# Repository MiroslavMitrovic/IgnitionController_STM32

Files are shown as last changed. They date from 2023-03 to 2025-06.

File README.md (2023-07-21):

# IgnitionController_STM32

## Ignition controller implementation for  4T Single Cylinder/V-Twin motorcycle. 

- Generated documentation is available in .\IgnitionController_STM32\Documentation\Ignition_Controller.chm
- Requirements are available in .\IgnitionController_STM32\Design\Requirements\IgnitionControllerRequriements.txt
- Architecture is done with Rational Software architect, and project is available at .\IgnitionController_STM32\Design\

## Addition of CMake build toolchain 
- Command for build configuration generation is : 
cmake -G "Unix Makefiles" -S . -B build -DCMAKE_BUILD_TYPE="Debug" -DCMAKE_TOOLCHAIN_FILE="arm-none-eabi-gcc.cmake" -DCMAKE_EXPORT_COMPILE_COMMANDS=1 
- Command for build is : 
cmake --build build
## Addition of Static and Dynamic Test Frameworks 
- For Static Code Analysis Mathworks Polyspace Code Prover and Bug finder tools are used 
- For Dynamic(Unit) Testing Google Test Framework is used 
- Setup is available in Testing Folder.

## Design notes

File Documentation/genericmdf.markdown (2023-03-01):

Design Document
===============
Project:Ignition Controller \n
Version: v1.00.00 \n

Table of Contents
-----------------

@subpage Description

@subpage TermsAndAbbreviations 

@subpage Resources 

@subpage Exceptions 

@subpage Tests 

@subpage Links 

@page Description
Description 
==============================

# Ignition Controller for 2 Cylinder Bike
Ignition controller powered by STM32F407VGT6 MCU. 
## Implementation 
-	RPM is calculated out of Sensor input from Crank or Cam shaft
-	Firing of cylinders is performed in scheduled manner via FSM handling.
## Architecture Display 
### File Structure
@image html IgnitionController_IgnitionControlerFileStructure.png
### Dependencies
@image html IgnitionController_IgnitionControlerStructure.png
### Activity Diagram 
@image html IgnitionController_IgnitionControllerActivityDiagram.png
### FSM Diagrams 
@image html IgnitionController_StatemachineDiagram1.png
@image html IgnitionController_StatemachineDiagram1_1.png
### Class Diagram
@image html IgnitionController_IgnitonControllerClasses.png
### Use Case Diagram 
@image html IgnitionController_UsecaseDiagram_IgnitionControl.png

@page TermsAndAbbreviations
Terms And Abbreviations 
=============================
**Ignition Controller is licensed under the GNU General Public License v3.0**
Permissions of this strong copyleft license are conditioned on making available complete source code of licensed works and modifications, which include larger works using a licensed work, under the same license. Copyright and license notices must be preserved. Contributors provide an express grant of patent rights.

####Permissions
-	Commercial use
-	 Modification
-	 Distribution
-	Patent use
-	 Private use
####Limitations
-	 x Liability
-	 x Warranty

@page Resources
Resources
============================
**RAM Consumption**
- 1.79kB used out of 128kB

**ROM Consumption**

- 17.51kB used out of 1024kB 

@page Exceptions
Exception and Error Handling
============================
If error occurs error handler will put MCU in infinite loop and application will not function.

@page Tests
# Dynamic Tests
- Dynamic Tests are available in folder Testing/Dynamic Testing. GTEST framework is used for unit testing. 
============================

@page Links 
**Links**
-  Link to the repo is [Ignition Controller](https://github.com/MiroslavMitrovic/IgnitionController_STM32.git).

============================

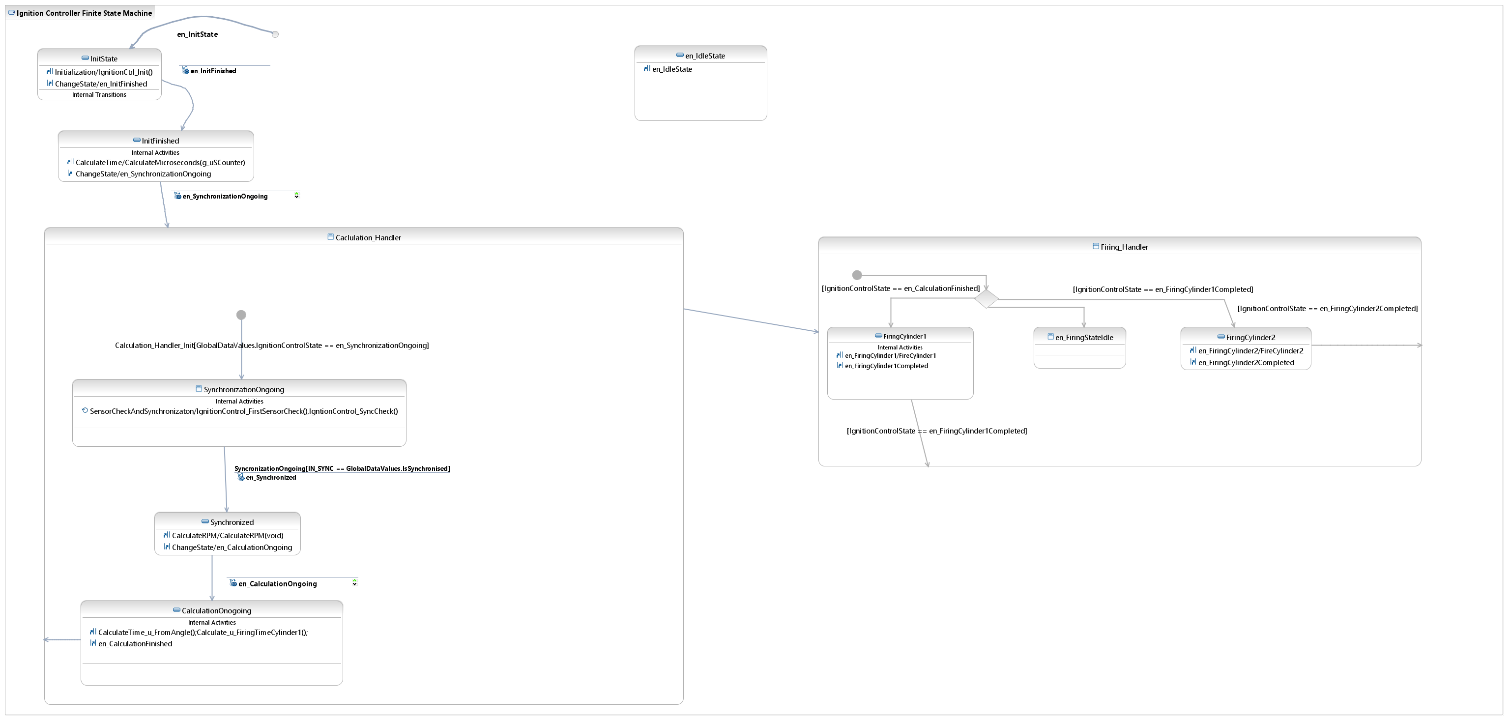
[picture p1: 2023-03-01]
Design/IgnitionController_IgnitionControllerFiniteStateMachineDiagram.png

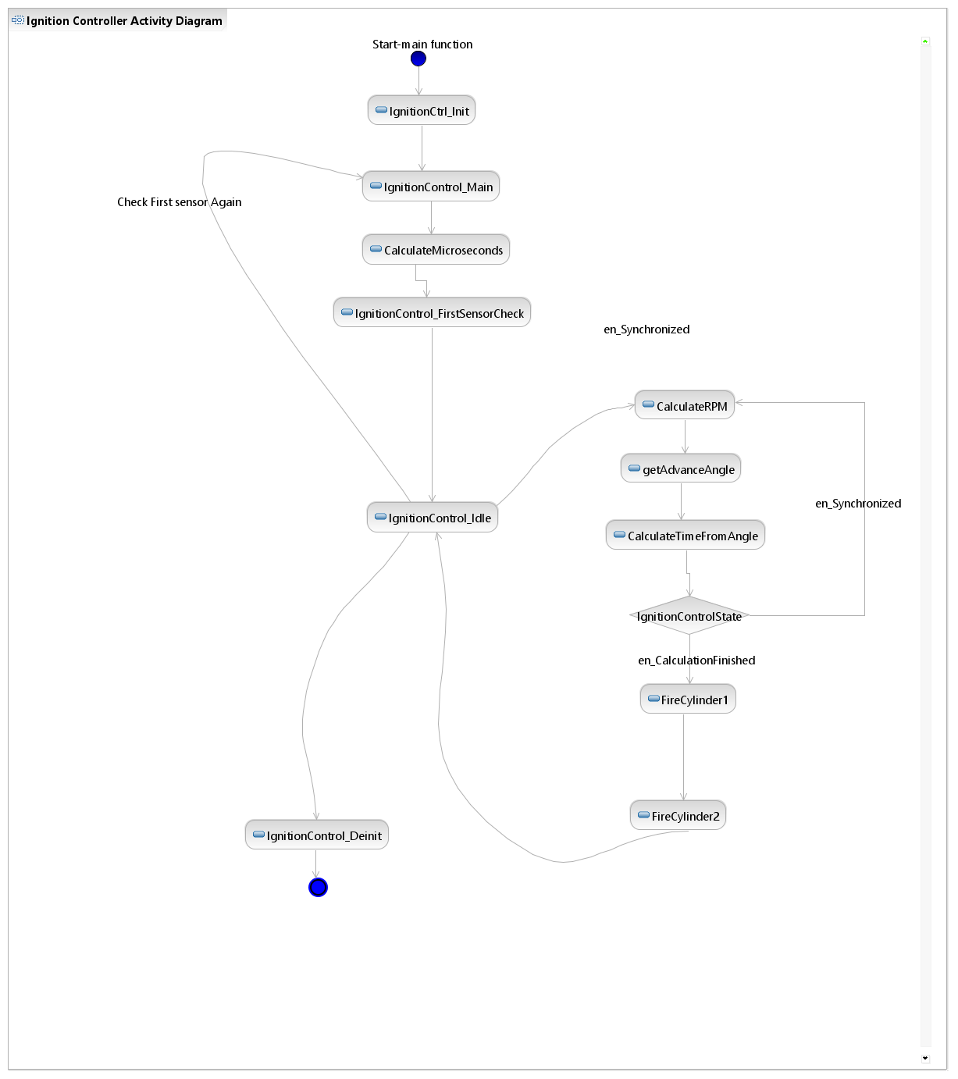
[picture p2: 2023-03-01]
Design/IgnitionController_IgnitionControllerActivityDiagram.png

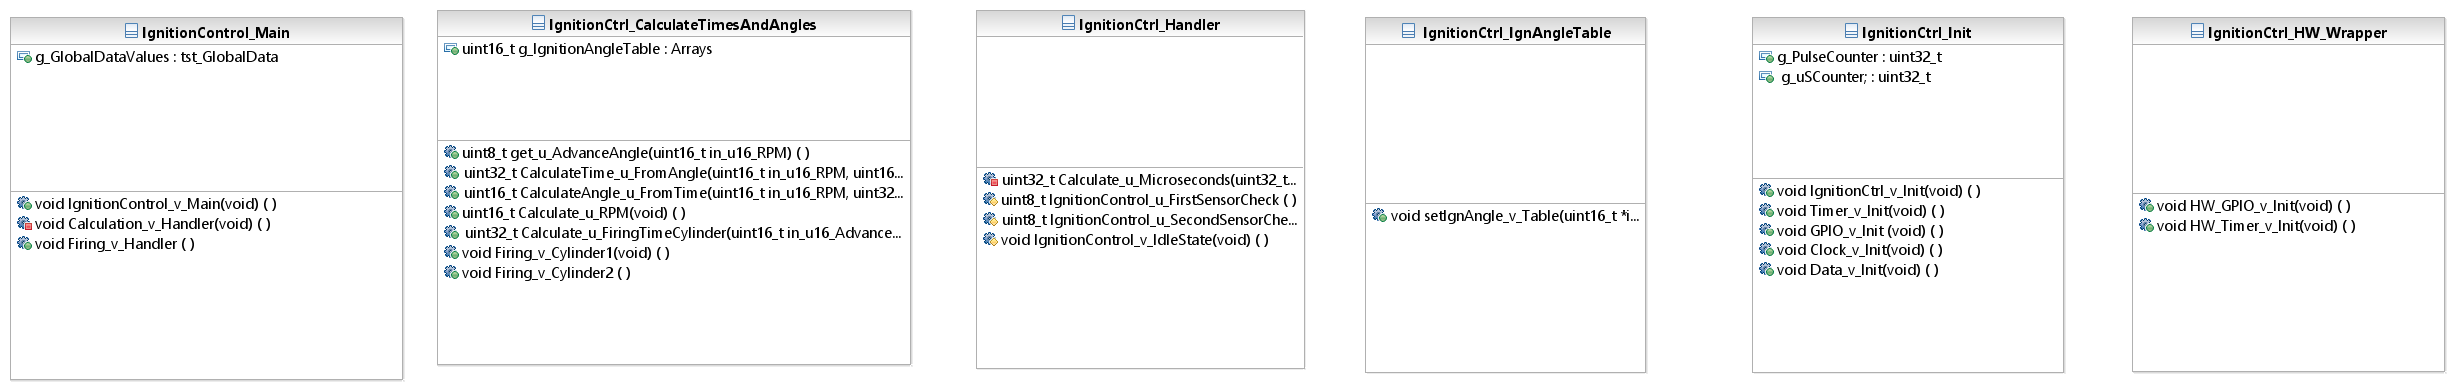
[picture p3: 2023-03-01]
Design/IgnitionController_IgnitonControllerClasses.png

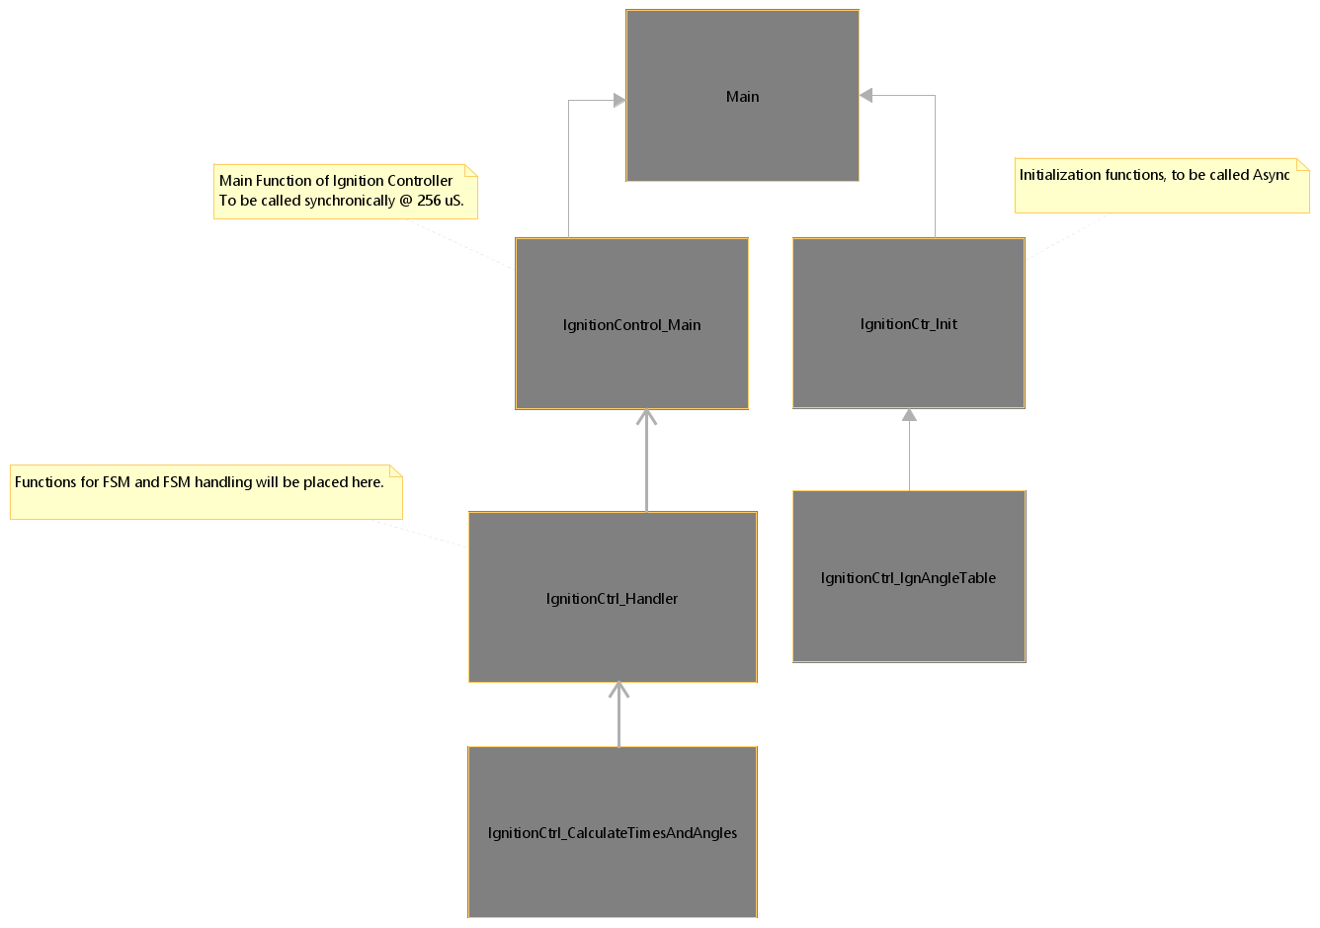
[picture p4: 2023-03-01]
Design/IgnitionController_IgnitionControlerStructure.png

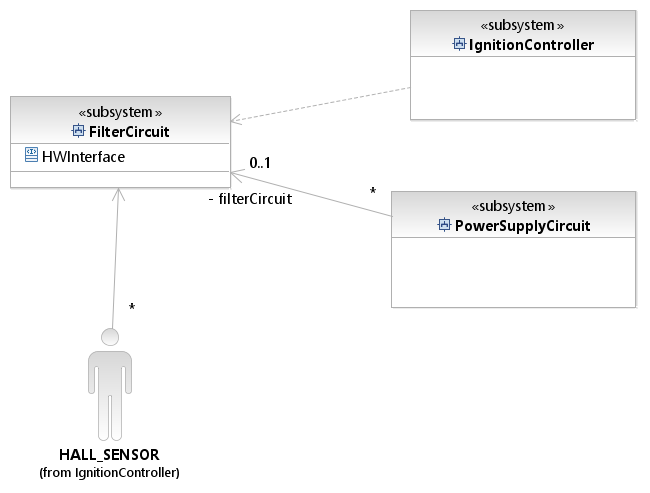
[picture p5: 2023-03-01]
Design/IgnitionController_UsecaseDiagram_IgnitionControl.png

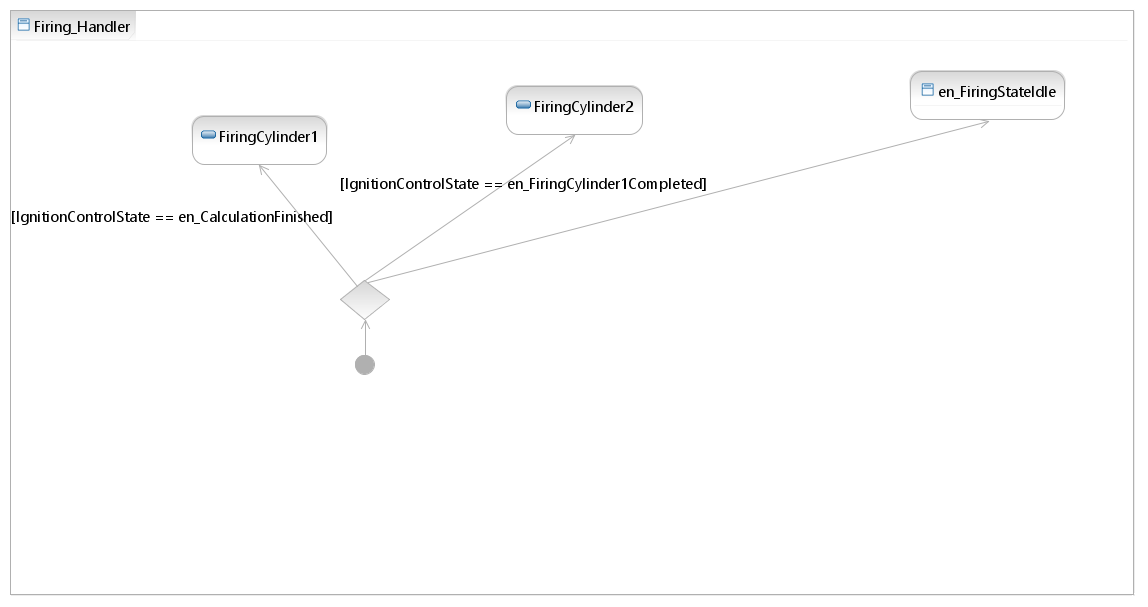
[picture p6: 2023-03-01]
Design/IgnitionController_StatemachineDiagram1_1.png

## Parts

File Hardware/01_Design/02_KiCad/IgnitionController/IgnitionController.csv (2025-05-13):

Reference | Qty | Value | DNP | Exclude from BOM | Exclude from Board | Footprint | Datasheet
C1,C2,C3,C4,C5,C13 | 6 | 100n |  |  |  | Capacitor_SMD:C_0805_2012Metric_Pad1.18x1.45mm_HandSolder | ~
C6,C9,C11 | 3 | UCL1V101MNL1GS |  |  |  | Capacitor_SMD:CP_Elec_8x11.9 | ~
C7 | 1 | 100u |  |  |  | Capacitor_SMD:C_0805_2012Metric_Pad1.18x1.45mm_HandSolder | ~
C8,C10,C12 | 3 | UCL1V331MNL1GS |  |  |  | Capacitor_SMD:CP_Elec_10x12.5 | ~
C14,C15 | 2 | 22p |  |  |  | Capacitor_SMD:C_0805_2012Metric_Pad1.18x1.45mm_HandSolder | ~
C16,C17,C18,C19 | 4 | 12p |  |  |  | Capacitor_SMD:C_0805_2012Metric_Pad1.18x1.45mm_HandSolder | ~
C20,C22,C24,C26,C28,C30,C32,C34,C36,C40,C42 | 11 | 0.1u |  |  |  | Capacitor_SMD:C_0805_2012Metric_Pad1.18x1.45mm_HandSolder | ~
C21,C23,C25,C27,C29,C31,C33,C35,C39,C41 | 10 | 1u |  |  |  | Capacitor_SMD:C_0805_2012Metric_Pad1.18x1.45mm_HandSolder | ~
C37,C38 | 2 | 2.2uF |  |  |  | Capacitor_SMD:C_0805_2012Metric_Pad1.18x1.45mm_HandSolder | ~
D3,D4,D5,D19,D20,D21,D22 | 7 | RED |  |  |  | LED_SMD:LED_1206_3216Metric_Pad1.42x1.75mm_HandSolder | ~
D6,D7,D17,D18 | 4 | SM6T100A |  |  |  | Diode_SMD:D_SMB | https://www.st.com/resource/en/datasheet/sm6t.pdf
D8 | 1 | BZX84B16VLY |  |  |  | Package_TO_SOT_SMD:SOT-23 | https://diotec.com/tl_files/diotec/files/pdf/datasheets/bzx84c2v4.pdf
D9,D13,D15 | 3 | SS14 |  |  |  | Diode_SMD:D_SMA | https://www.vishay.com/docs/88746/ss12.pdf
D10 | 1 | KDZV18B |  |  |  | Diode_SMD:D_SOD-123 | ~
D11,D14,D16 | 3 | RED |  |  |  | LED_SMD:LED_0805_2012Metric_Pad1.15x1.40mm_HandSolder | ~
D12 | 1 | BZX84C18VLY |  |  |  | Package_TO_SOT_SMD:SOT-23 | https://diotec.com/tl_files/diotec/files/pdf/datasheets/bzx84c2v4.pdf
F1 | 1 | 2A Fuse |  |  |  | Fuse:Fuse_0805_2012Metric_Pad1.15x1.40mm_HandSolder | ~
L3,L4,L5 | 3 | L_Iron |  |  |  | Inductor_SMD:L_7.3x7.3_H3.5 | ~
Q1,Q7 | 2 | SS8050 |  |  |  | Package_TO_SOT_SMD:TSOT-23_HandSoldering | http://www.secosgmbh.com/datasheet/products/SSMPTransistor/SOT-23/SS8050.pdf
Q2,Q3 | 2 | DMP6050SSD |  |  |  | Package_SO:SOIC-8_3.9x4.9mm_P1.27mm | https://www.diodes.com/assets/Datasheets/DMP6050SSD.pdf
Q4 | 1 | RSJ250P10 |  |  |  | Package_TO_SOT_SMD:TO-263-2 | https://ngspice.sourceforge.io/docs/ngspice-html-manual/manual.xhtml#cha_MOSFETs
Q5 | 1 | BC856 |  |  |  | Package_TO_SOT_SMD:SOT-23 | https://www.onsemi.com/pub/Collateral/BC860-D.pdf
Q6 | 1 | IRF9Z34NSPbF |  |  |  | Package_TO_SOT_SMD:TO-263-2 | https://ngspice.sourceforge.io/docs/ngspice-html-manual/manual.xhtml#cha_MOSFETs
Q8,Q9,Q10,Q11 | 4 | IRF540N |  |  |  | Package_TO_SOT_THT:TO-220-3_Vertical | http://www.irf.com/product-info/datasheets/data/irf540n.pdf
R1,R4,R28 | 3 | 10k |  |  |  | Resistor_SMD:R_0805_2012Metric_Pad1.20x1.40mm_HandSolder | ~
R2 | 1 | 510R |  |  |  | Resistor_SMD:R_0805_2012Metric_Pad1.20x1.40mm_HandSolder | ~
R3,R16,R17,R18,R19 | 5 | 0R |  |  |  | Resistor_SMD:R_0805_2012Metric_Pad1.20x1.40mm_HandSolder | ~
R5,R6,R7,R15 | 4 | 475R |  |  |  | Resistor_SMD:R_0805_2012Metric_Pad1.20x1.40mm_HandSolder | ~
R8,R33,R35,R36,R37,R38,R40,R41,R46,R47,R52,R53 | 12 | 10K |  |  |  | Resistor_SMD:R_0805_2012Metric_Pad1.20x1.40mm_HandSolder | ~
R9 | 1 | 169K |  |  |  | Resistor_SMD:R_0815_2038Metric_Pad1.20x4.05mm_HandSolder | ~
R10 | 1 | 5K |  |  |  | Resistor_SMD:R_0805_2012Metric_Pad1.20x1.40mm_HandSolder | ~
R11,R14,R42,R43,R44,R57 | 6 | 470R |  |  |  | Resistor_SMD:R_0805_2012Metric_Pad1.20x1.40mm_HandSolder | ~
R12,R39 | 2 | 1M |  |  |  | Resistor_SMD:R_0805_2012Metric_Pad1.20x1.40mm_HandSolder | ~
R13 | 1 | 47.5K |  |  |  | Resistor_SMD:R_0805_2012Metric_Pad1.20x1.40mm_HandSolder | ~
R20,R21,R22 | 3 | 8.2K |  |  |  | Resistor_SMD:R_0805_2012Metric_Pad1.20x1.40mm_HandSolder | ~
R23 | 1 | 8.2K1 |  |  |  | Resistor_SMD:R_0815_2038Metric_Pad1.20x4.05mm_HandSolder | ~
R24,R26,R30,R32 | 4 | 69K8 |  |  |  | Resistor_SMD:R_0805_2012Metric_Pad1.20x1.40mm_HandSolder | ~
R25,R27,R29,R31 | 4 | 12K1 |  |  |  | Resistor_SMD:R_0805_2012Metric_Pad1.20x1.40mm_HandSolder | ~
R34,R45 | 2 | 43k |  |  |  | Resistor_SMD:R_0805_2012Metric_Pad1.20x1.40mm_HandSolder | ~
R48,R49 | 2 | 360R |  |  |  | Resistor_SMD:R_0805_2012Metric_Pad1.20x1.40mm_HandSolder | ~
R50,R51,R60,R65 | 4 | 2K |  |  |  | Resistor_SMD:R_0805_2012Metric_Pad1.20x1.40mm_HandSolder | ~
R54,R55,R56,R59,R61,R62,R63,R64 | 8 | 100R |  |  |  | Resistor_SMD:R_0805_2012Metric_Pad1.20x1.40mm_HandSolder | ~
TP1 | 1 | PMIC_CLK |  |  |  | TestPoint:TestPoint_Plated_Hole_D2.0mm | ~
TP2 | 1 | SPI_CS |  |  |  | TestPoint:TestPoint_Plated_Hole_D2.0mm | ~
TP3 | 1 | SPI_MOSI |  |  |  | TestPoint:TestPoint_Plated_Hole_D2.0mm | ~
TP4 | 1 | SPI_MISO |  |  |  | TestPoint:TestPoint_Plated_Hole_D2.0mm | ~
TP5 | 1 | SPI_SCK |  |  |  | TestPoint:TestPoint_Plated_Hole_D2.0mm | ~
TP6 | 1 | KL30_ADC |  |  |  | TestPoint:TestPoint_Plated_Hole_D2.0mm | ~
TP7 | 1 | KL15_ADC |  |  |  | TestPoint:TestPoint_Plated_Hole_D2.0mm | ~
TP8 | 1 | VSEN_ADC |  |  |  | TestPoint:TestPoint_Plated_Hole_D2.0mm | ~
TP9 | 1 | VMCU_ADC |  |  |  | TestPoint:TestPoint_Plated_Hole_D2.0mm | ~
TP10 | 1 | Cyl1_TP |  |  |  | TestPoint:TestPoint_Plated_Hole_D2.0mm | ~
TP11 | 1 | Cyl2_TP |  |  |  | TestPoint:TestPoint_Plated_Hole_D2.0mm | ~
TP12 | 1 | Sig1_TP |  |  |  | TestPoint:TestPoint_Plated_Hole_D2.0mm | ~
TP13 | 1 | Sig2_TP |  |  |  | TestPoint:TestPoint_Plated_Hole_D2.0mm | ~
TP14 | 1 | Cyl3_TP |  |  |  | TestPoint:TestPoint_Plated_Hole_D2.0mm | ~
TP15 | 1 | Cyl4_TP |  |  |  | TestPoint:TestPoint_Plated_Hole_D2.0mm | ~
U1 | 1 | ATmega328PB-A |  |  |  | Package_QFP:TQFP-32_7x7mm_P0.8mm | http://ww1.microchip.com/downloads/en/DeviceDoc/40001906C.pdf
U2,U5,U6,U7 | 4 | 4N35 |  |  |  | Library:SMD-6_7 | https://www.vishay.com/docs/81181/4n35.pdf
U3 | 1 | LM2575-3.3BU |  |  |  | Package_TO_SOT_SMD:TO-263-5_TabPin3 | http://ww1.microchip.com/downloads/en/DeviceDoc/lm2575.pdf
U4,U9 | 2 | LM2575-5.0BU |  |  |  | Package_TO_SOT_SMD:TO-263-5_TabPin3 | http://ww1.microchip.com/downloads/en/DeviceDoc/lm2575.pdf
U8,U25 | 2 | TXS0104EPW |  |  |  | Package_SO:TSSOP-14_4.4x5mm_P0.65mm | www.ti.com/lit/ds/symlink/txs0104e.pdf
U10,U11 | 2 | TLV2372 |  |  |  | Package_SO:SOIC-8_5.3x6.2mm_P1.27mm | http://www.ti.com/lit/ds/symlink/tlv2375.pdf
U12 | 1 | STM32F407VGTx |  |  |  | Package_QFP:LQFP-100_14x14mm_P0.5mm | https://www.st.com/resource/en/datasheet/stm32f407vg.pdf
U14 | 1 | AT24CS01-SSHM |  |  |  | Package_SO:SOIC-8_3.9x4.9mm_P1.27mm | http://ww1.microchip.com/downloads/en/DeviceDoc/Atmel-8815-SEEPROM-AT24CS01-02-Datasheet.pdf
U15 | 1 | MCP2557FD-xSN |  |  |  | Package_SO:SOIC-8_3.9x4.9mm_P1.27mm | https://ww1.microchip.com/downloads/en/DeviceDoc/20005533A.pdf
U19,U20 | 2 | IXDN602 |  |  |  | Package_SO:SO-8_3.9x4.9mm_P1.27mm
U23,U24 | 2 | 4N35 |  |  |  | Package_DIP:DIP-6_W7.62mm | https://www.vishay.com/docs/81181/4n35.pdf
Y1 | 1 | 16MHz |  |  |  | Crystal:Crystal_HC52-8mm_Horizontal | ~
Y2 | 1 | 32.768kHz |  |  |  | Crystal:Crystal_HC52-8mm_Horizontal | ~
Y3 | 1 | 8MHz |  |  |  | Crystal:Crystal_HC52-8mm_Horizontal | ~

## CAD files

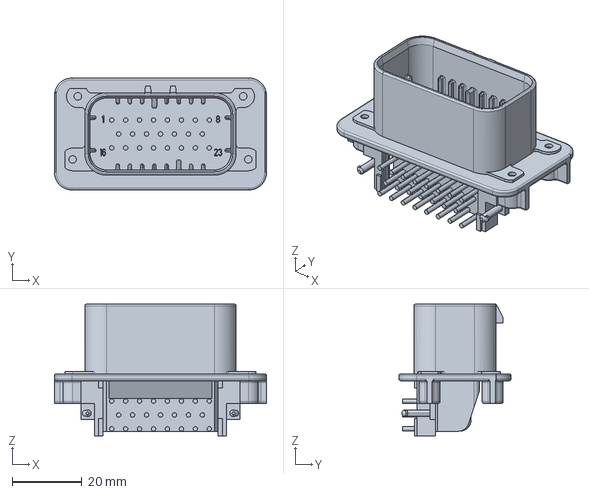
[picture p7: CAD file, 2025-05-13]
Hardware/02_Parts/02_Models/LIB_770669-1/770669-1/3D/770669-1.stp
60.8 x 32.1 x 37.8 mm

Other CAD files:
Hardware/01_Design/02_KiCad/IgnitionController/Pins.step.SLDPRT
Hardware/01_Design/02_KiCad/IgnitionController/Body.step.SLDPRT
Hardware/02_Parts/02_Models/FTSH-105-01-L-DV-A/Allegro/ftsh-105-xx-yyy-dv-a.psm
Hardware/02_Parts/02_Models/FTSH-105-01-L-DV-A/DEHDL/ftsh_105_01_l_dv_a/chips/chips.prt
Hardware/02_Parts/02_Models/LIB_770669-1/770669-1/Allegro/7706691.psm
Hardware/02_Parts/02_Models/LIB_770669-1/770669-1/DEHDL/770669_1/chips/chips.prt

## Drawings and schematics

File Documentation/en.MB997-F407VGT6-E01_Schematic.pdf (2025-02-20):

Title: Project overview

Size:

Reference:
A4 | Sheet: | of

Revision:

Project: STM32F407G-DISC1

E 01 | MB997

F407VGT6

Date:

Variant:

Table of contents | Legend

General comment such as function title, configuration, ...

Text to be added to silkscreen.

Sheet 1: Project overview (this page)

Sheet 2: Top

# STM32F407G-DISC1

MB997

Sheet 3: ST-LINK/V2-A (SWD only)

Sheet 4: Peripherals

Sheet 7: MCU

Sheet 6: Audio

Sheet 6: USB_OTG_FS

Warning text.

# Open Platform License Agreement

The Open Platform License Agreement (“Agreement”) is a binding legal contract between you ("You")

and STMicroelectronics International N.V. (“ST”), a company incorporated under the laws of the

Netherlands acting for the purpose of this Agreement through its Swiss branch 39, Chemin du

Champ des Filles, 1228 Plan-les-Ouates, Geneva, Switzerland.

By using the enclosed reference designs, schematics, PC board layouts, and documentation, in hardcopy

or CAD tool file format (collectively, the “Reference Material”), You are agreeing to be bound by

the terms and conditions of this Agreement. Do not use the Reference Material until You have read

and agreed to this Agreement terms and conditions. The use of the Reference Material automatically

implies the acceptance of the Agreement terms and conditions.

The complete Open Platform License Agreement can be found on www.st.com/opla.

U_Top
Top.SchDoc

Notes to generate the
board layout.

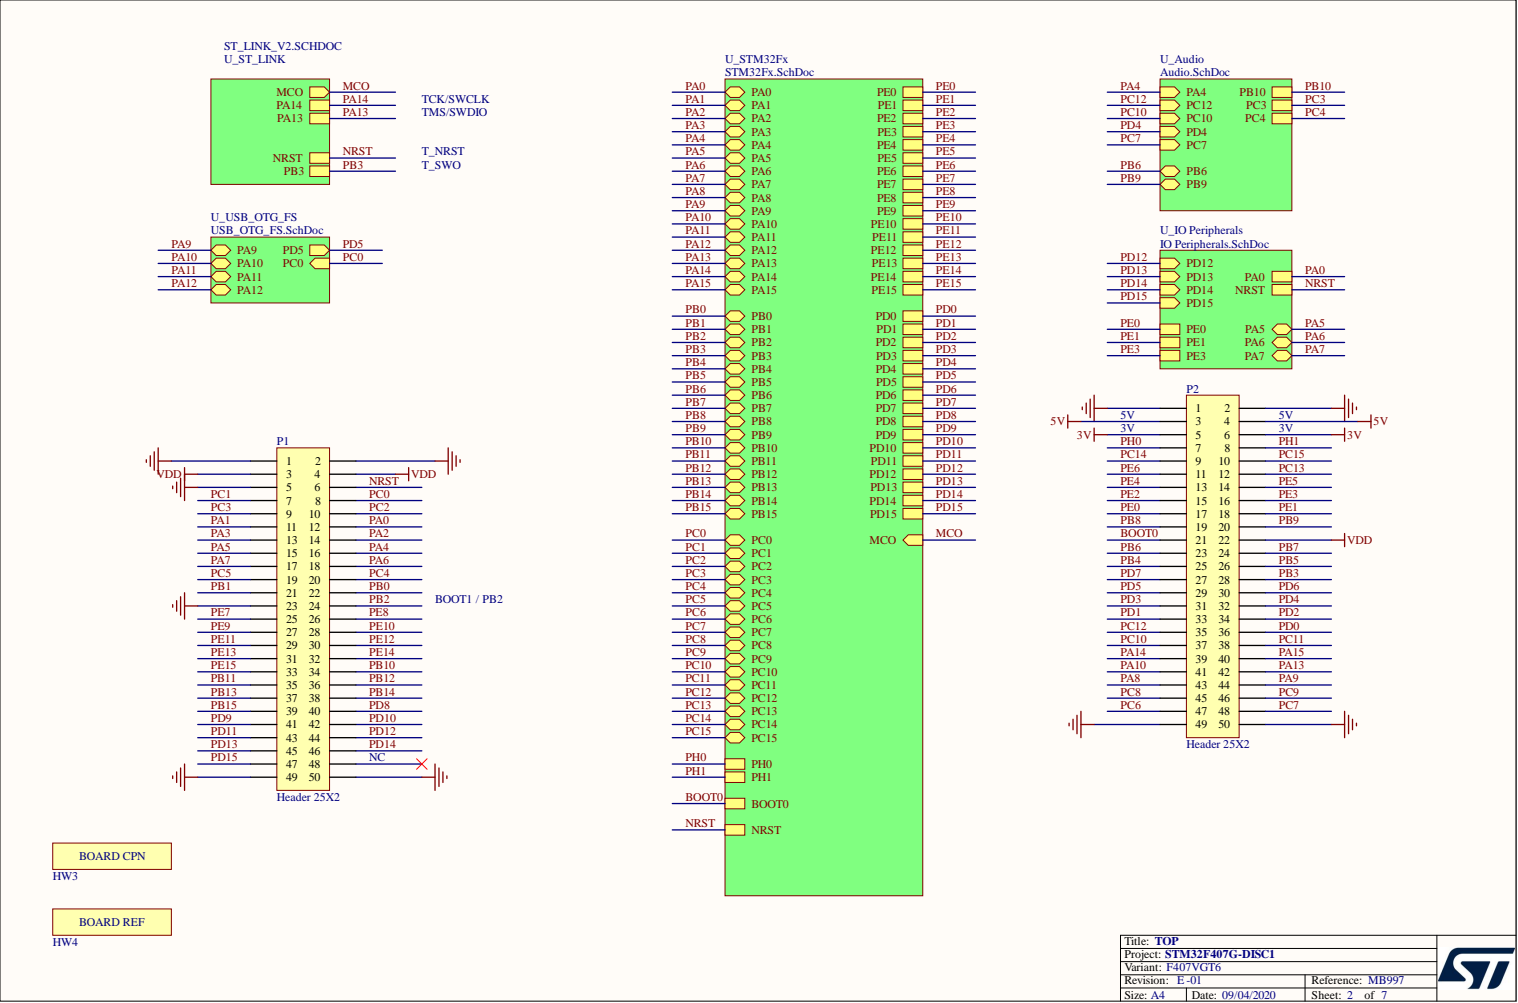
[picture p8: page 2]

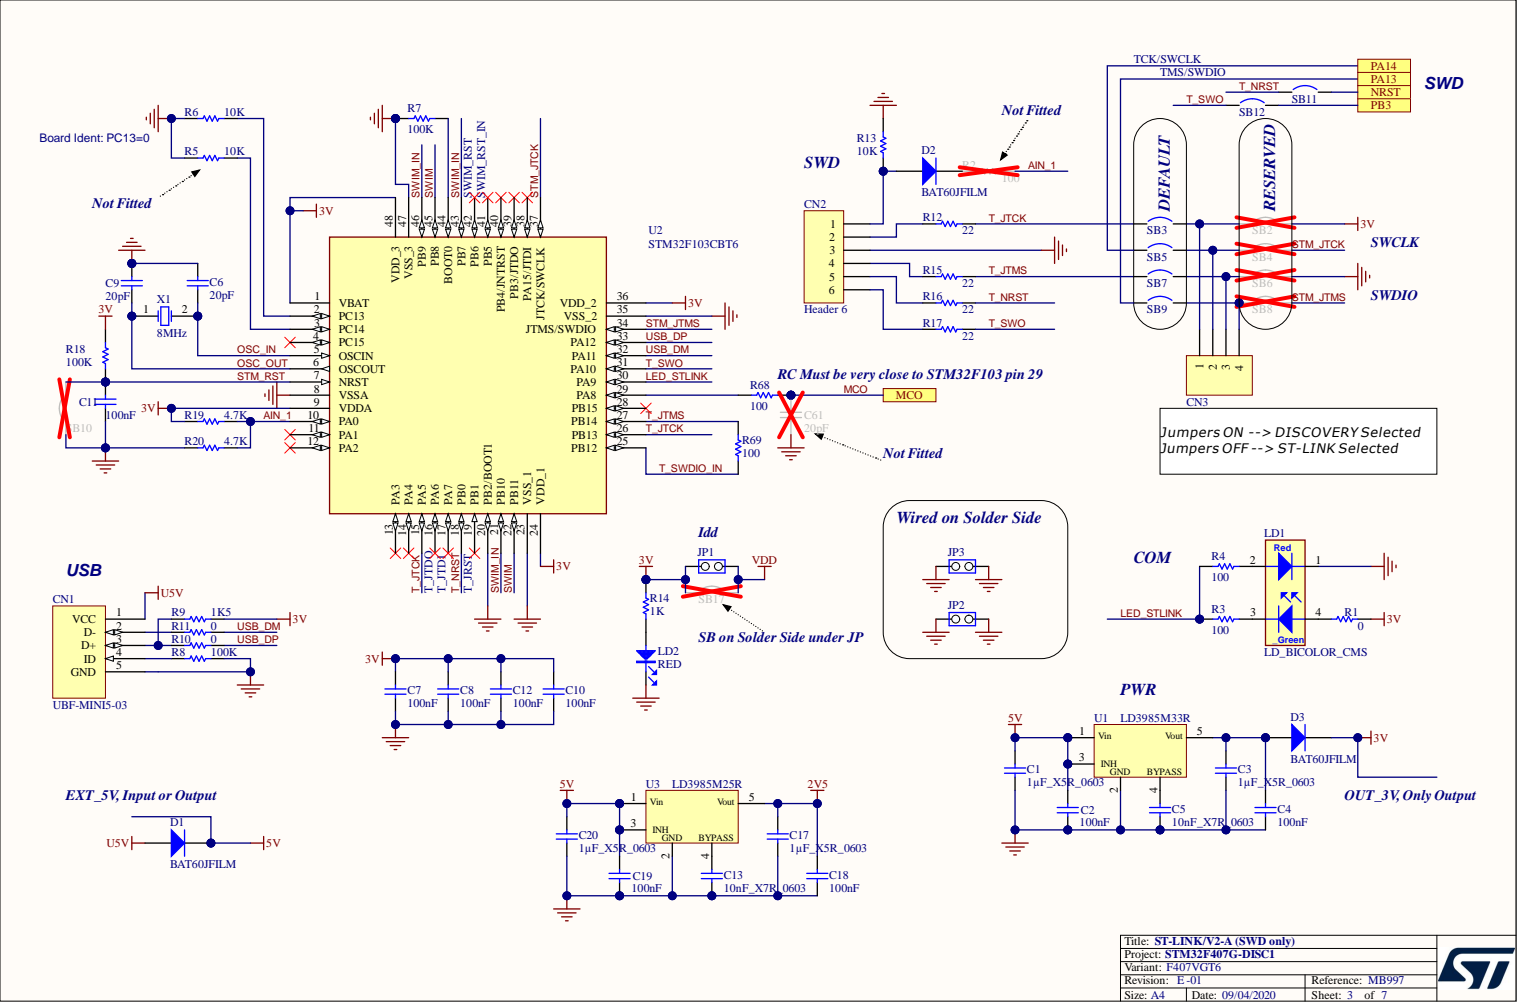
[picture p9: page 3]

RC Must be very close to STM32F103 pin 29

Jumpers ON --> DISCOVERY Selected
Jumpers OFF --> ST-LINK Selected

Wired on Solder Side

SB on Solder Side under JP

Title: ST-LINK/V2-A (SWD only)

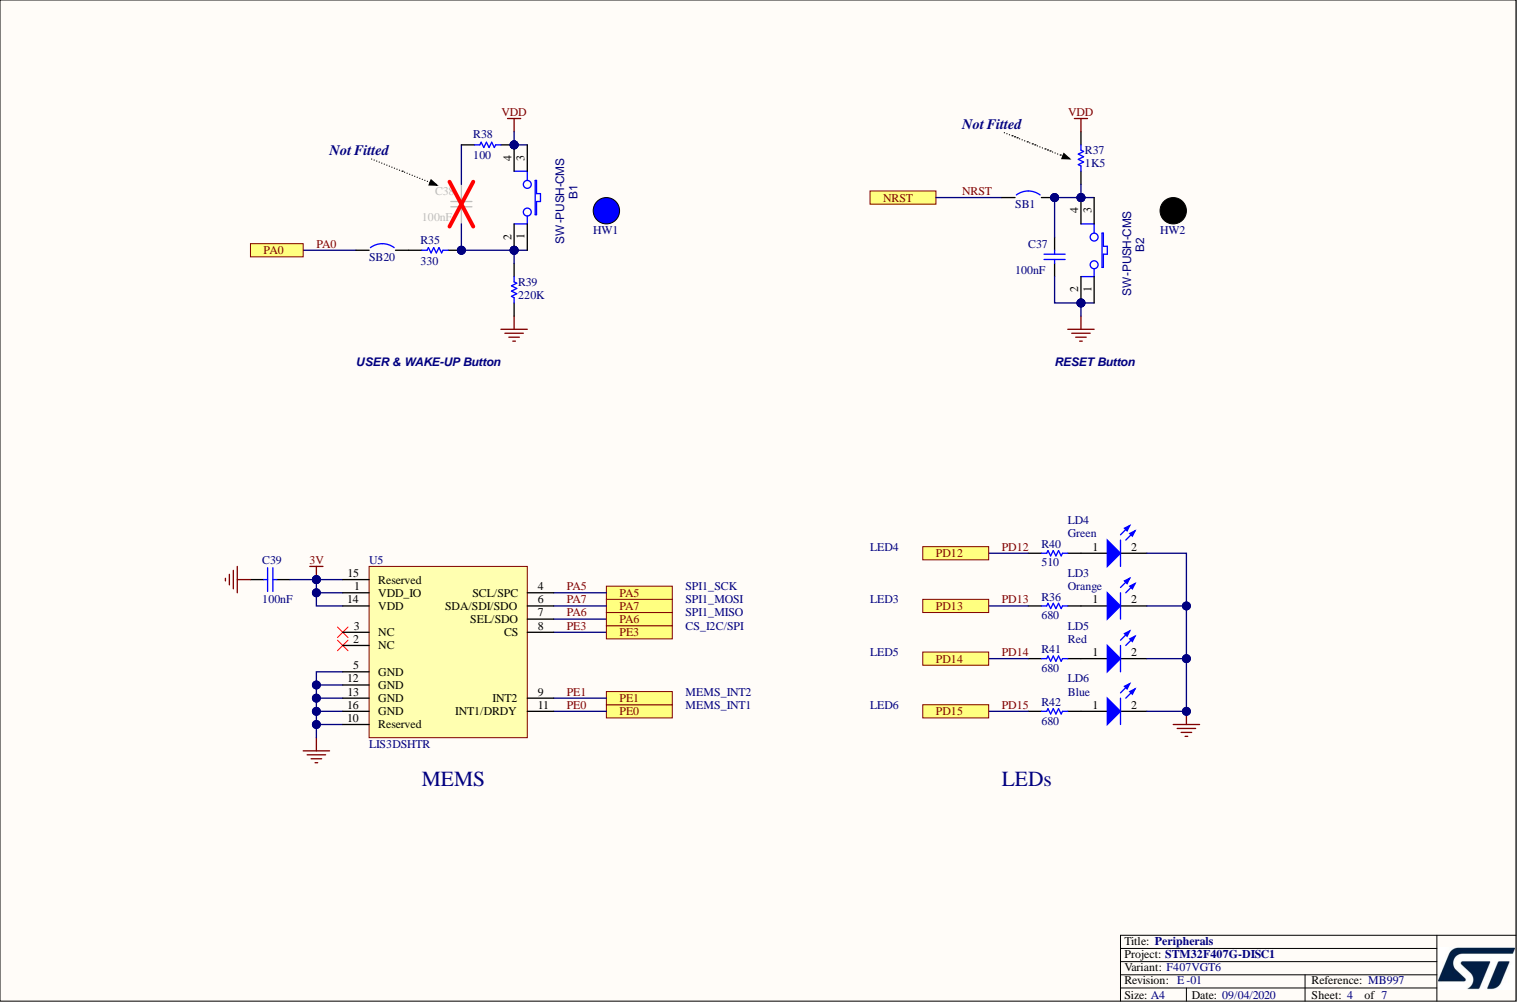
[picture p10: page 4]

USER & WAKE-UP Button

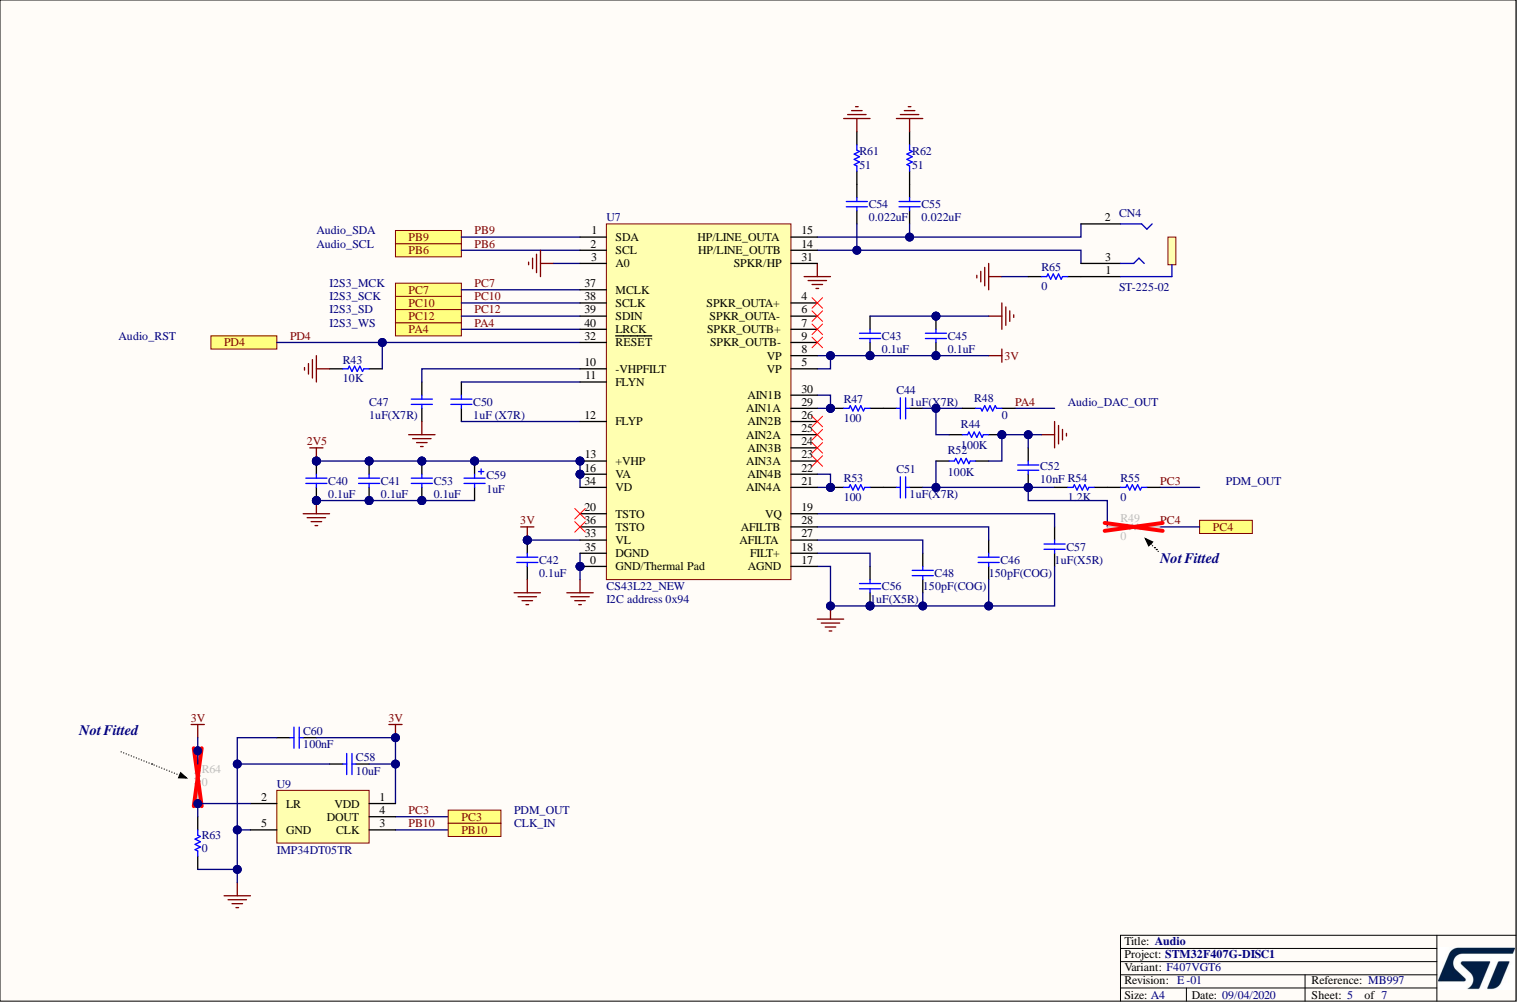
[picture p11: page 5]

-VHPFILT 10

FLYP 12

U9
LR 2

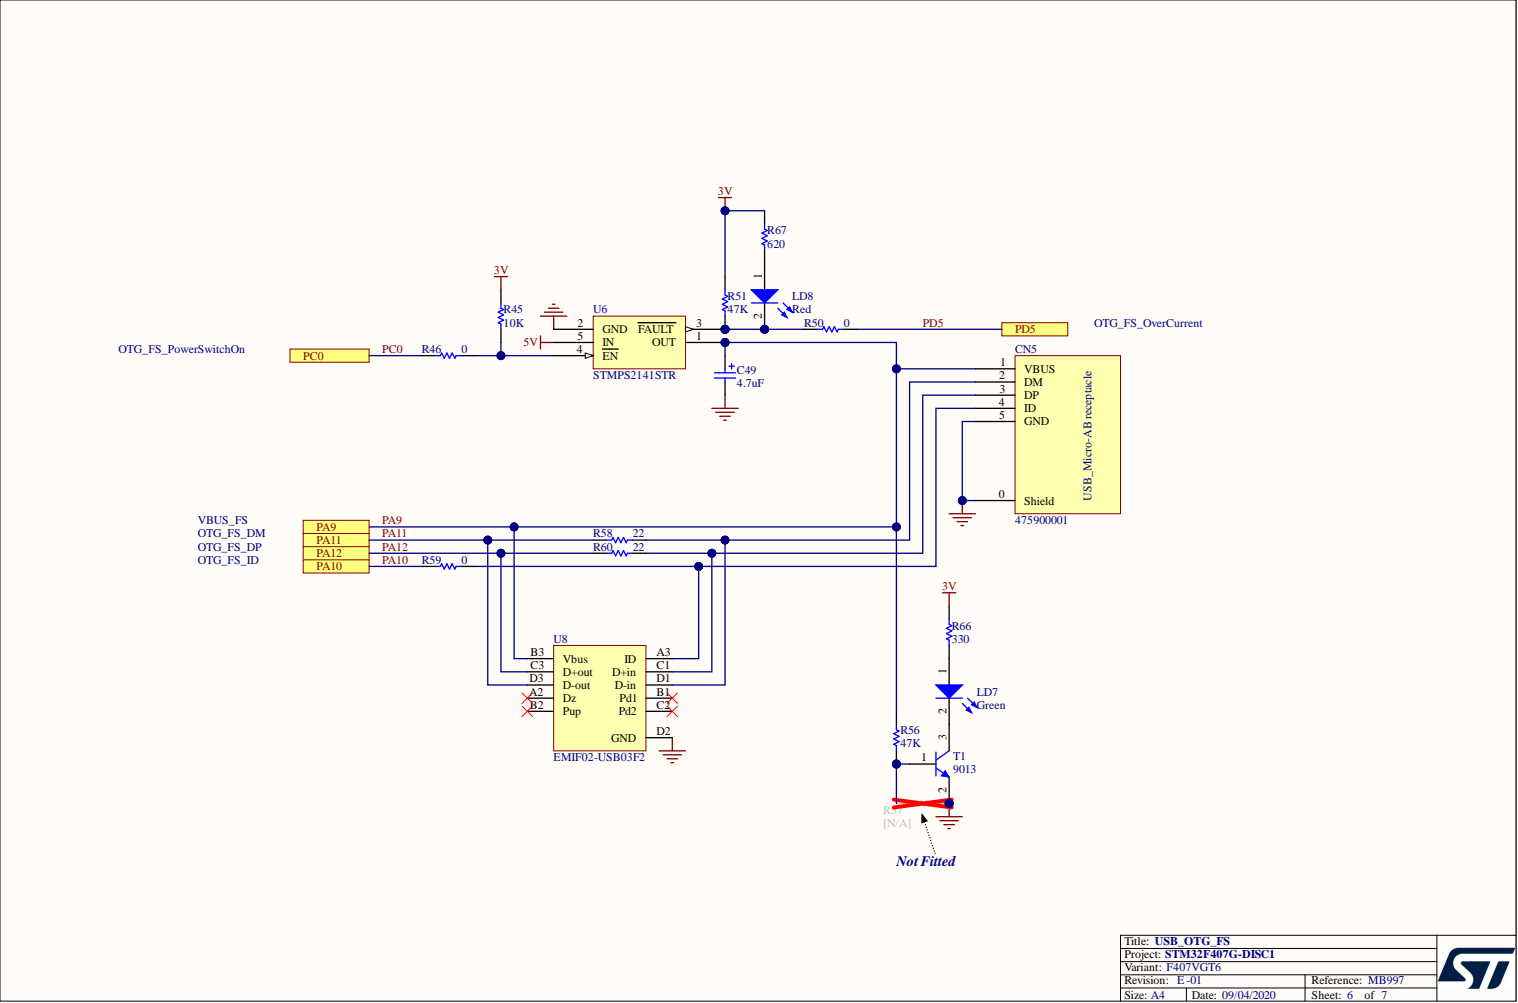
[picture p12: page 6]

STMPS2141STR C49 | | DM 2

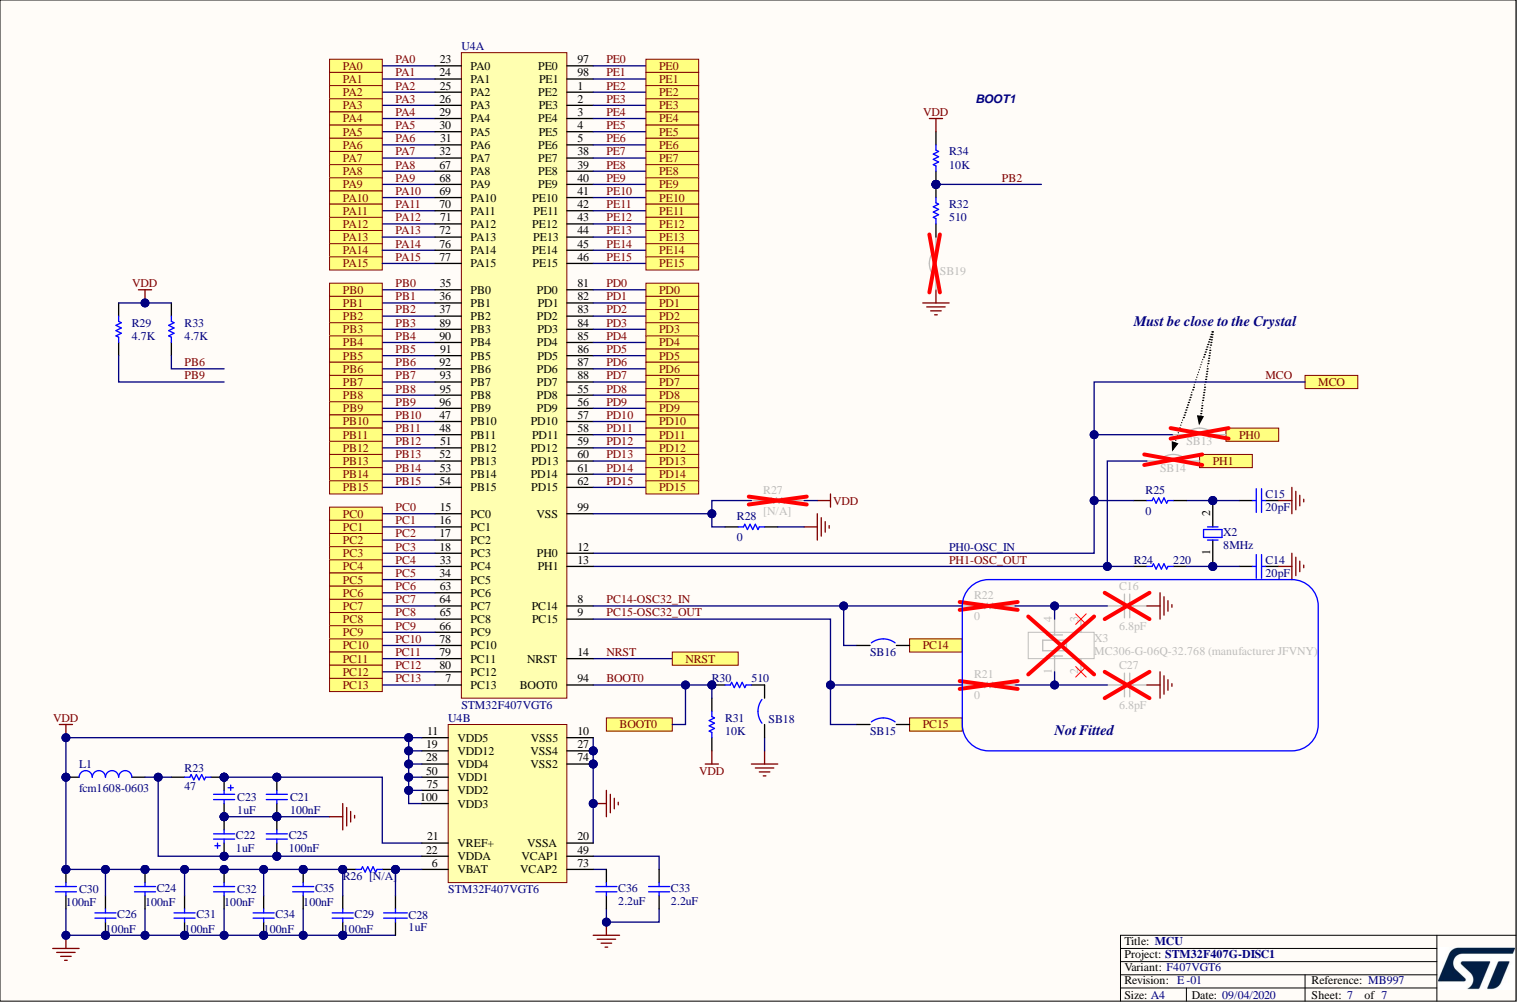
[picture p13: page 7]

PA2 | PA2 25 | | PE2
PA3 | PA3 26 | PE3
PA4 | PA4 29 | PE4
PA5 | PA5 30 | PE5
PA6 | PA6 31 | PE6
PA7 | PA7 32 | PE7
PA8 | PA8 67 | PE8
PA9 | PA9 68 | PE9
PA10 | PA10 69 | PE10
PA11 | PA11 70 | PE11
PA12 | PA12 71 | PE12
PA13 | PA13 72 | PE13
PA14 | PA14 76 | PE14
PA15 | PA15 77 | PE15

PA5 | | | | PE5
PA6 | | | | PE6

PA10 | | | | PE10
PA11 | | | | PE11

PB1 | PB1 36 | PD1
PB2 | PB2 37 | PD2
PB3 | PB3 89 | PD3
PB4 | PB4 90 | PD4
PB5 | PB5 91 | PD5

Must be close to the Crystal

PB4 | | | | PD4
PB5 | | | | PD5

PB8 | PB8 95 | PD8
PB9 | PB9 96 | PD9
PB10 | PB10 47 | PD10
PB11 | PB11 48 | PD11
PB12 | PB12 51 | | PD12
PB13 | PB13 52 | | PD13

PB9 | | | | PD9
PB10 | | | | PD10

C22 | C25
1uF | 100nF | VDDA 22

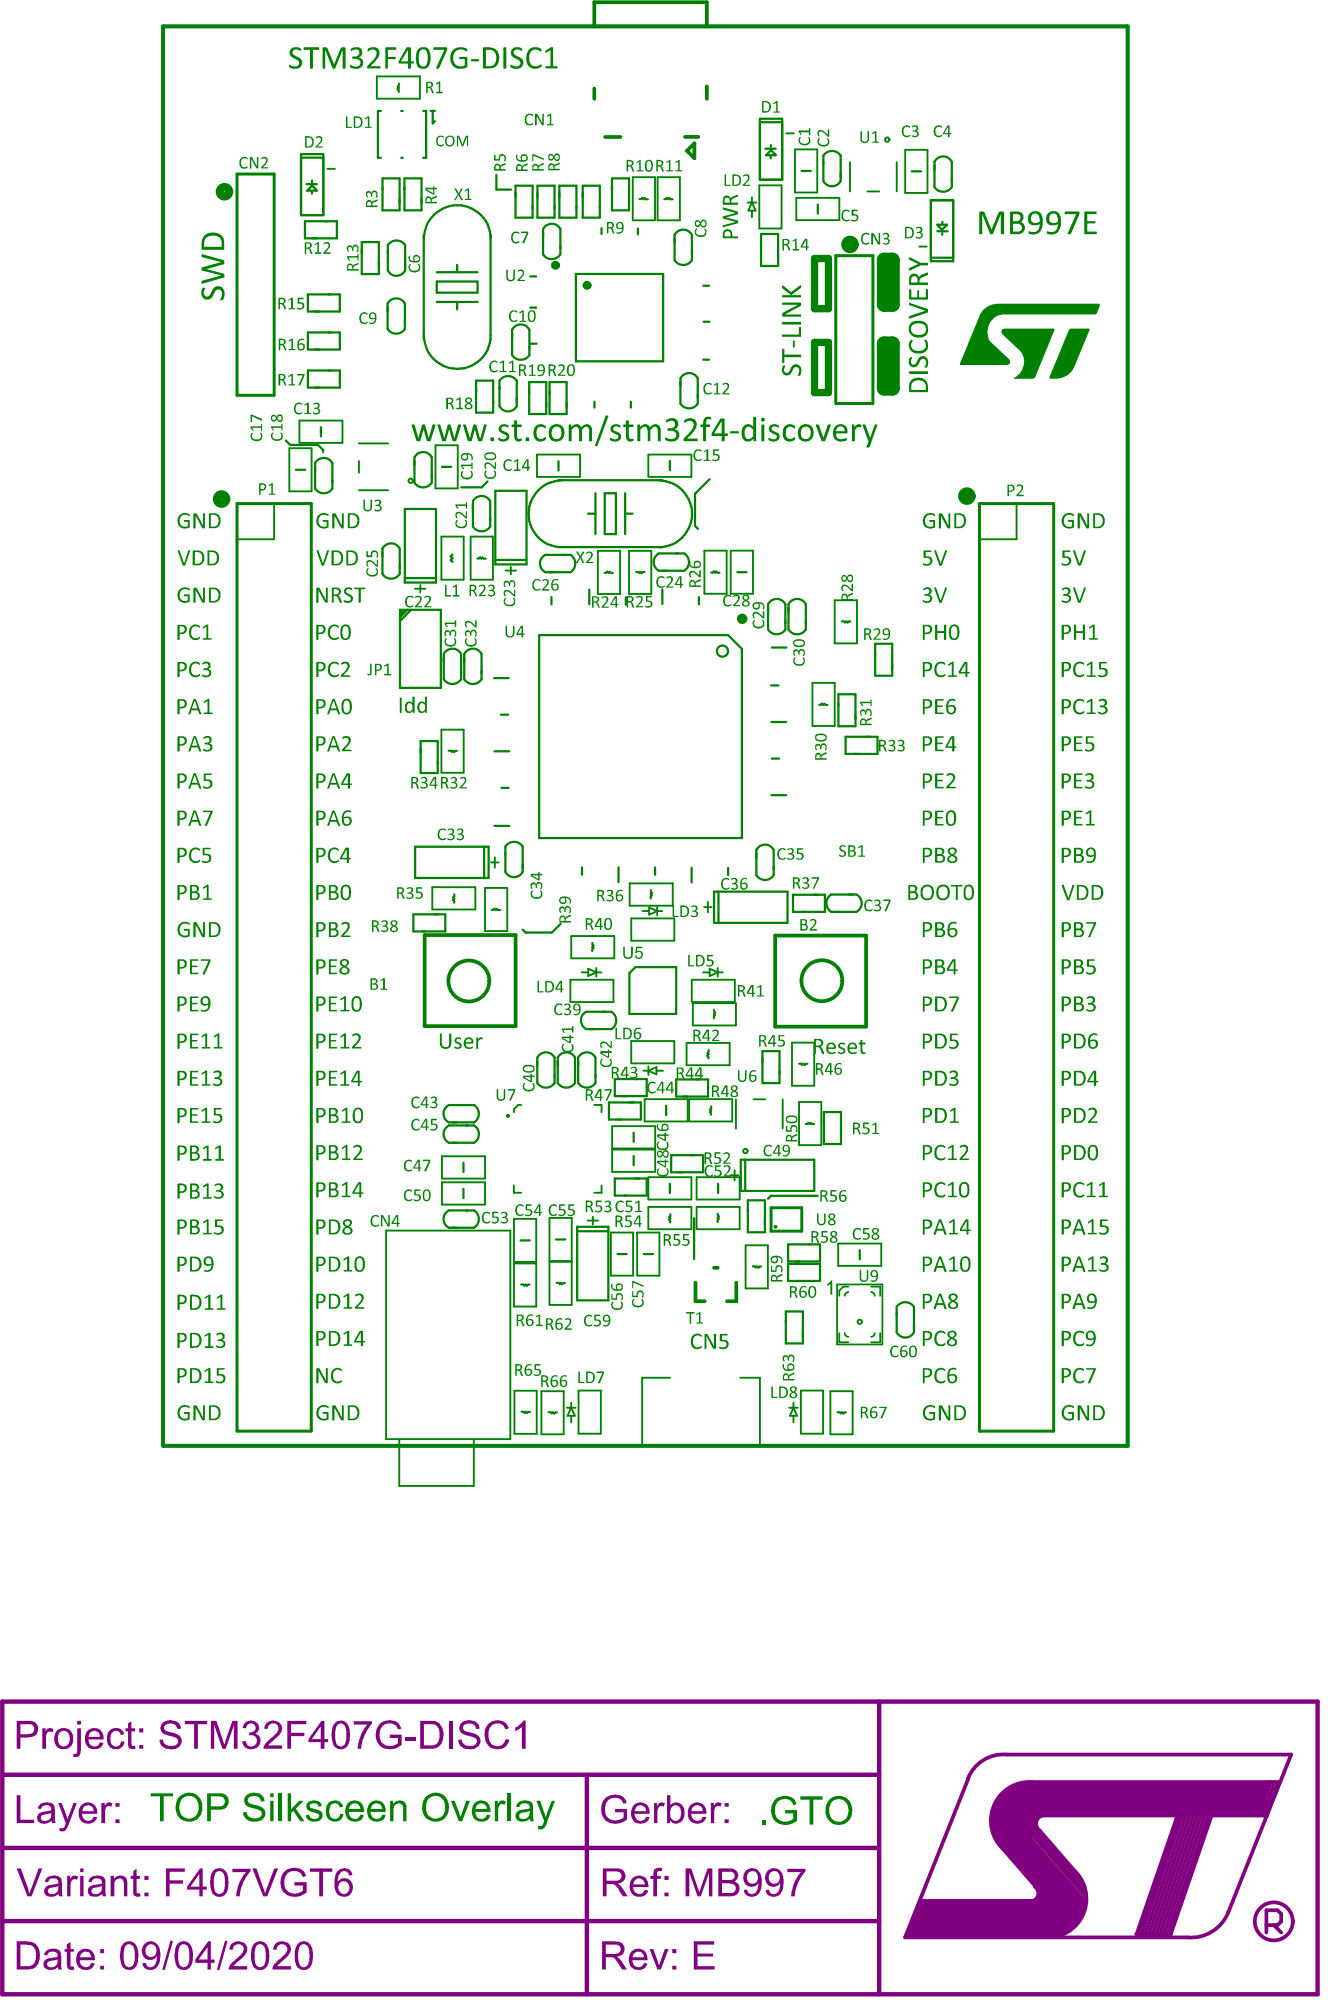
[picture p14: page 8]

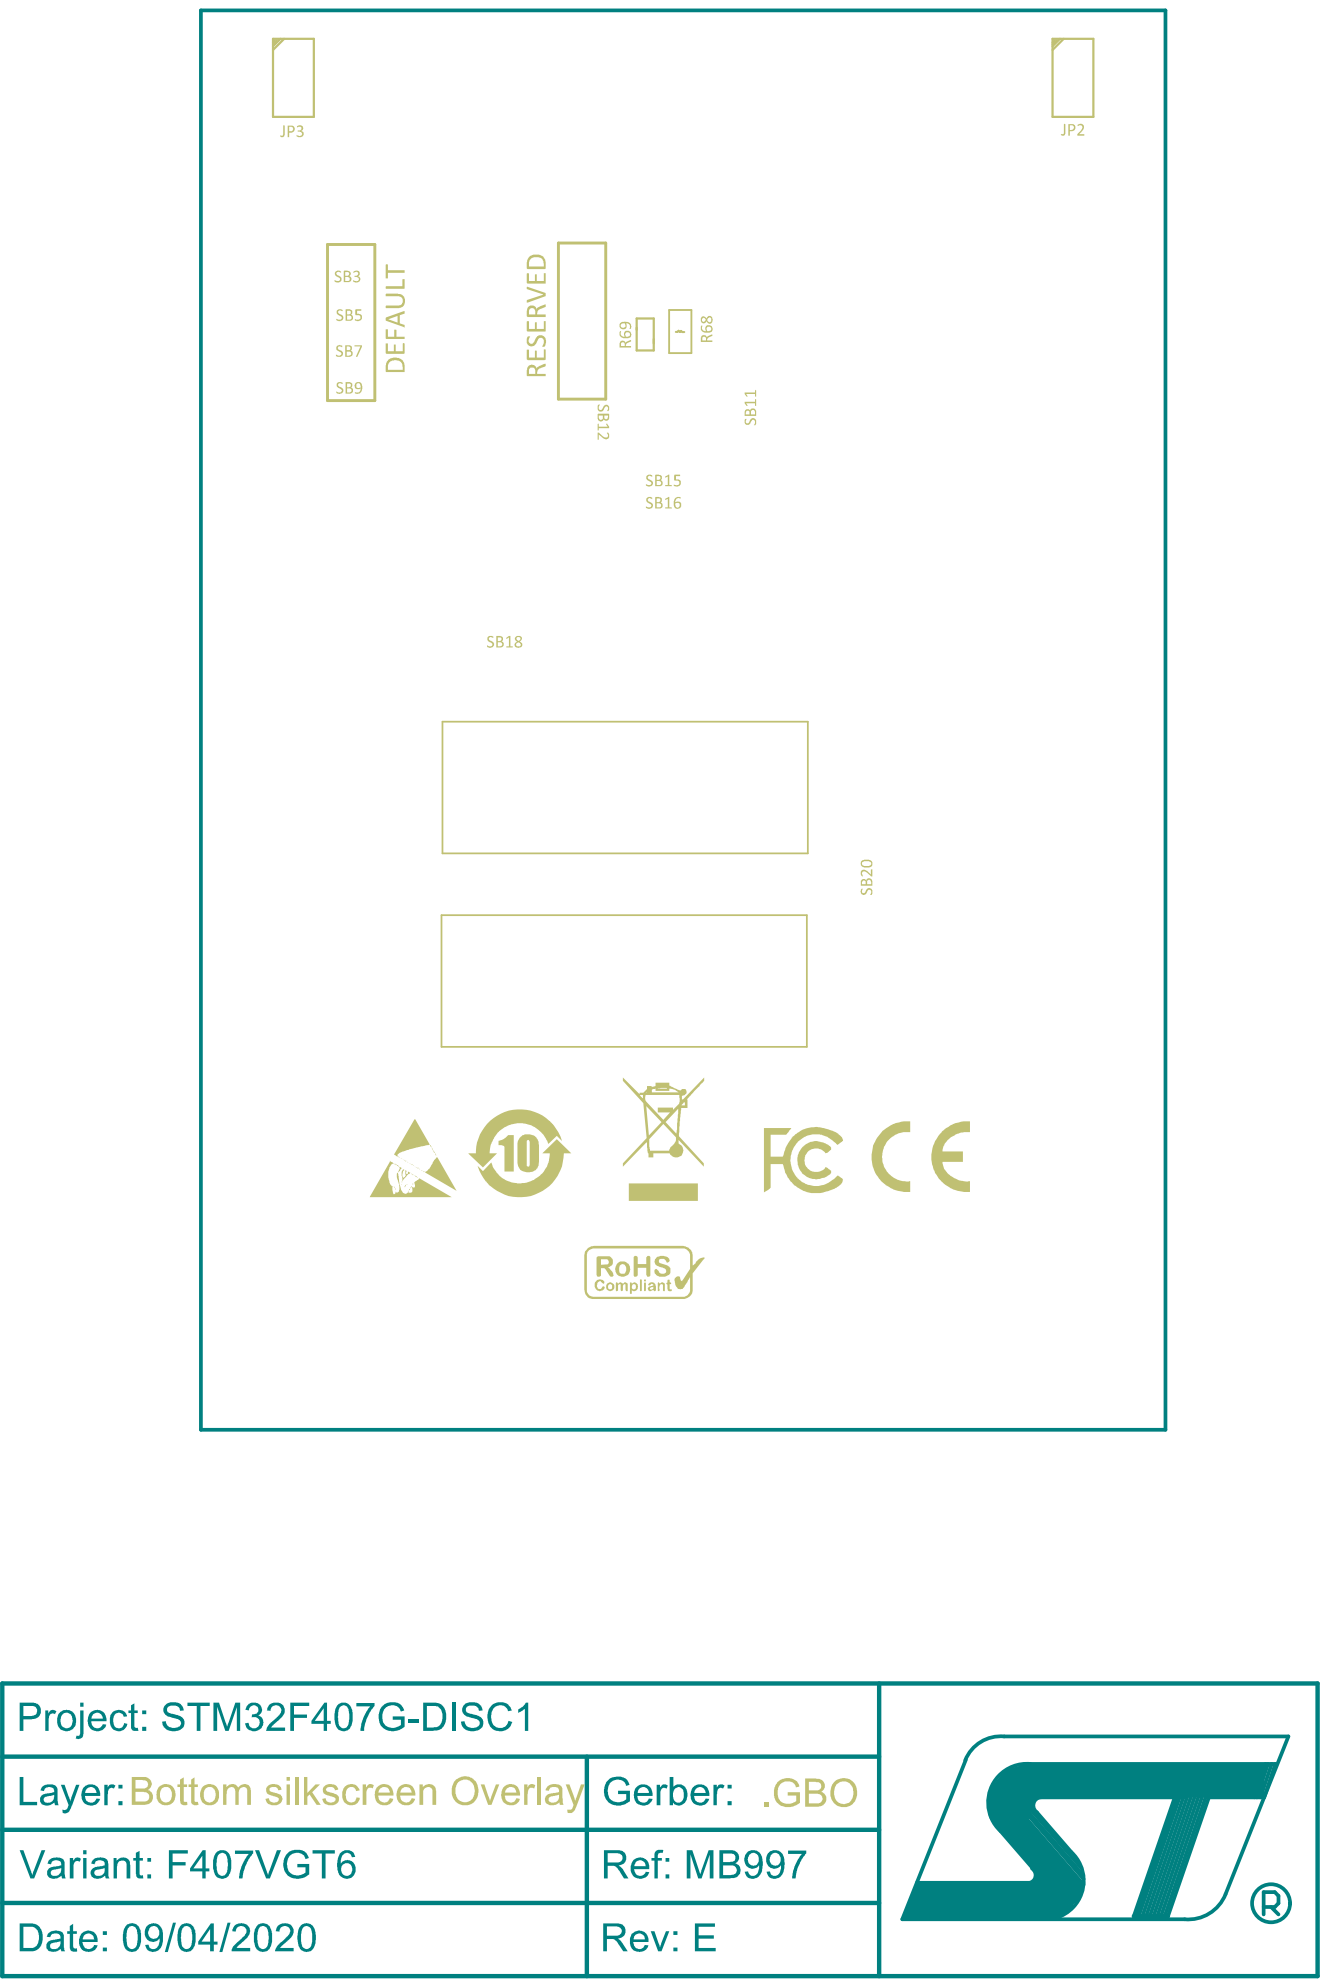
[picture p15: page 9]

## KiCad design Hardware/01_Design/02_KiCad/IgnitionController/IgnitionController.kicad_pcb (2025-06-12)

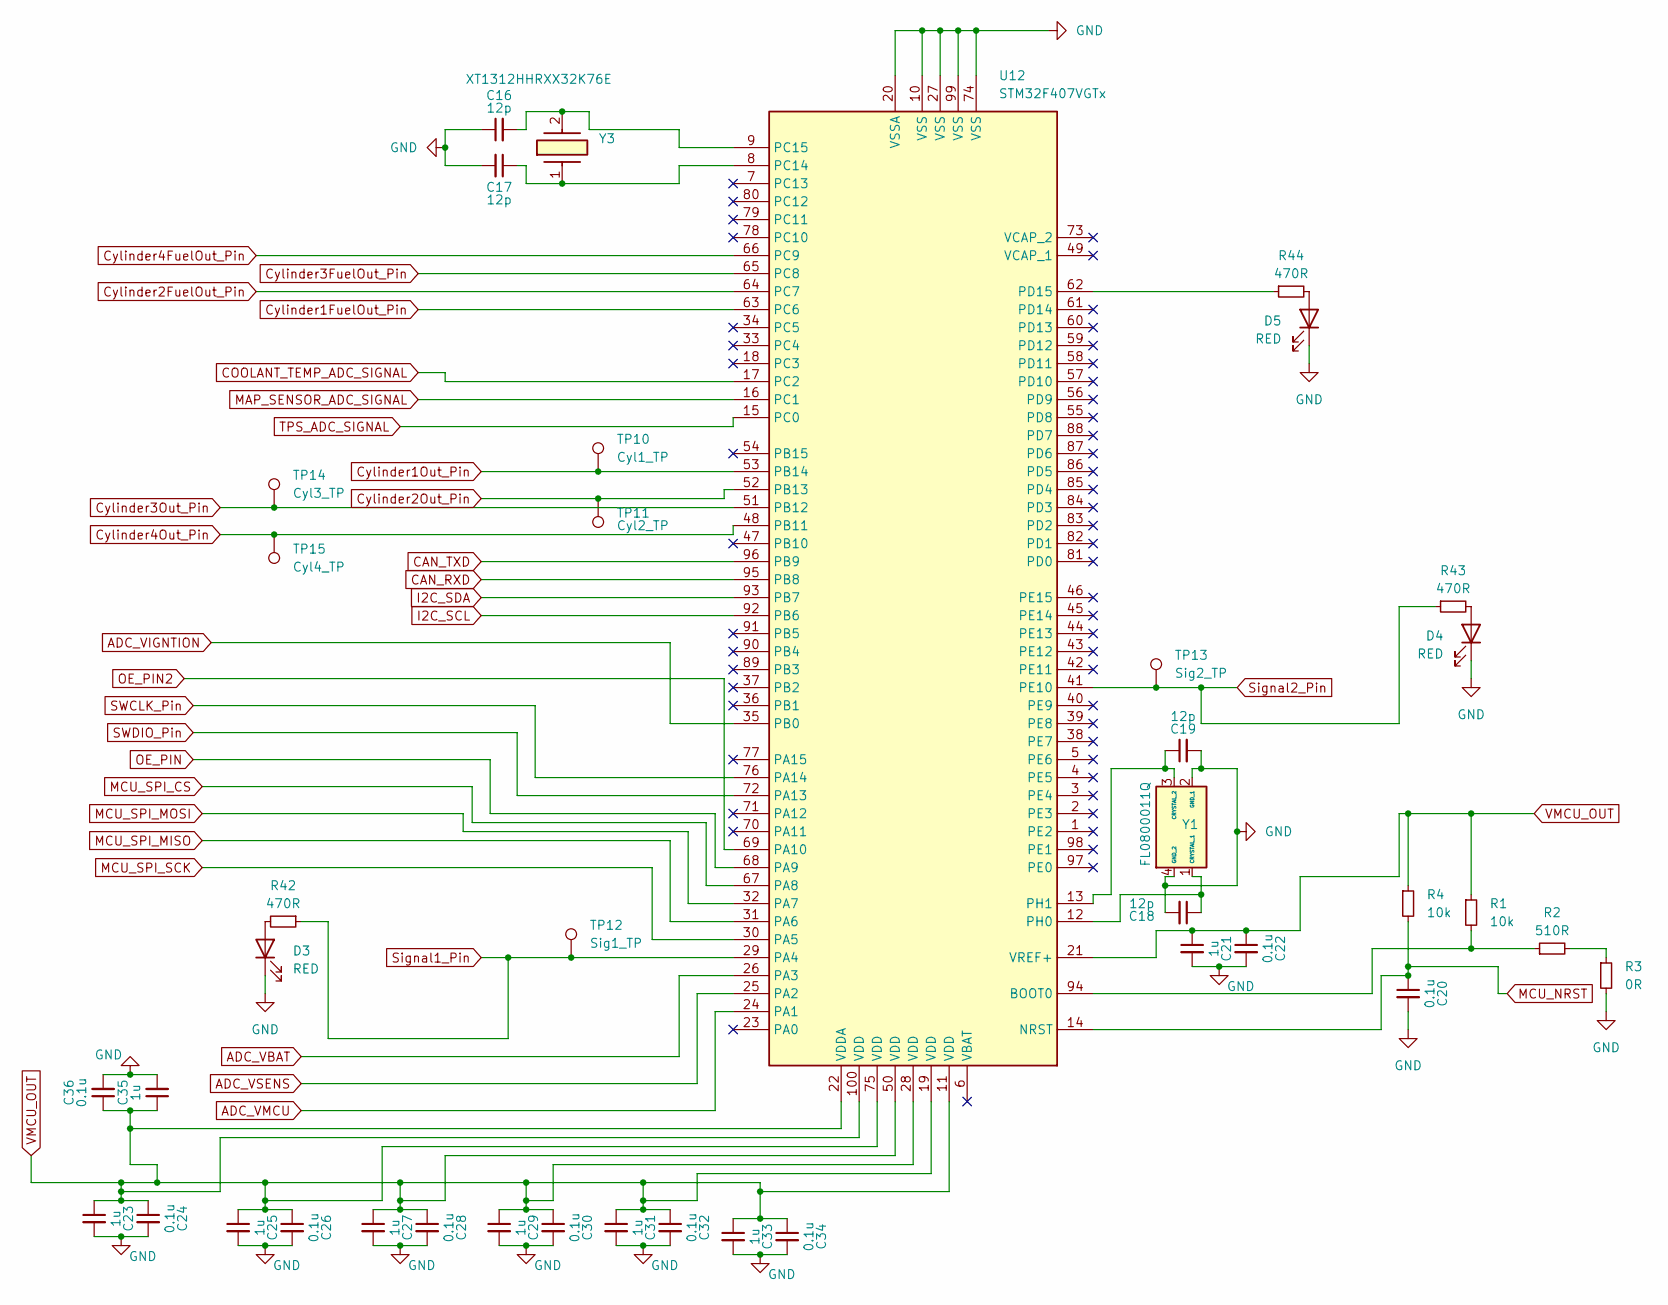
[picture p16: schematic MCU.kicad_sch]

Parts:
C16, C17, C18, C19: 12p; C_0603_1608Metric_Pad1.08x0.95mm_HandSolder
C20, C22, C24, C26, C28, C30, C32, C34, C36: 0.1u; C_0603_1608Metric_Pad1.08x0.95mm_HandSolder
C21, C23, C25, C27, C29, C31, C33, C35: 1u; C_0603_1608Metric_Pad1.08x0.95mm_HandSolder
D3, D4, D5: RED; LED_1206_3216Metric_Pad1.42x1.75mm_HandSolder
R1, R4: 10k; R_0603_1608Metric_Pad0.98x0.95mm_HandSolder
R2: 510R; R_0603_1608Metric_Pad0.98x0.95mm_HandSolder
R3: 0R; R_0603_1608Metric_Pad0.98x0.95mm_HandSolder
R42, R43, R44: 470R; R_0603_1608Metric_Pad0.98x0.95mm_HandSolder
TP10: Cyl1_TP; TestPoint_Pad_1.0x1.0mm
TP11: Cyl2_TP; TestPoint_Pad_1.0x1.0mm
TP12: Sig1_TP; TestPoint_Pad_1.0x1.0mm
TP13: Sig2_TP; TestPoint_Pad_1.0x1.0mm
TP14: Cyl3_TP; TestPoint_Pad_1.0x1.0mm
TP15: Cyl4_TP; TestPoint_Pad_1.0x1.0mm
U12: STM32F407VGTx; LQFP-100_14x14mm_P0.5mm
Y1: FL0800011Q; Mouser Part Number 729-FL0800011Q
Y3: XT1312HHRXX32K76E; Mouser Part Number 70-XT1312HHRXX32K76E

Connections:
ADC_VBAT: U12.26 (PA3); also elsewhere on the board
ADC_VIGNTION: U12.35 (PB0); also elsewhere on the board
ADC_VMCU: U12.24 (PA1); also elsewhere on the board
ADC_VSENS: U12.25 (PA2); also elsewhere on the board
CAN_RXD: U12.95 (PB8); also elsewhere on the board
CAN_TXD: U12.96 (PB9); also elsewhere on the board
COOLANT_TEMP_ADC_SIGNAL: U12.17 (PC2); also elsewhere on the board
Cylinder1FuelOut_Pin: U12.63 (PC6); also elsewhere on the board
Cylinder1Out_Pin: TP10.1, U12.53 (PB14); also elsewhere on the board
Cylinder2FuelOut_Pin: U12.64 (PC7); also elsewhere on the board
Cylinder2Out_Pin: TP11.1, U12.52 (PB13); also elsewhere on the board
Cylinder3FuelOut_Pin: U12.65 (PC8); also elsewhere on the board
Cylinder3Out_Pin: TP14.1, U12.51 (PB12); also elsewhere on the board
Cylinder4FuelOut_Pin: U12.66 (PC9); also elsewhere on the board
Cylinder4Out_Pin: TP15.1, U12.48 (PB11); also elsewhere on the board
I2C_SCL: U12.92 (PB6); also elsewhere on the board
I2C_SDA: U12.93 (PB7); also elsewhere on the board
MAP_SENSOR_ADC_SIGNAL: U12.16 (PC1); also elsewhere on the board
MCU_NRST: C20.1, R4.2, U12.14 (NRST); also elsewhere on the board
MCU_SPI_CS: U12.67 (PA8); also elsewhere on the board
MCU_SPI_MISO: U12.31 (PA6); also elsewhere on the board
MCU_SPI_MOSI: U12.32 (PA7); also elsewhere on the board
MCU_SPI_SCK: U12.30 (PA5); also elsewhere on the board
unnamed: D3.2 (A), R42.2
unnamed: D4.2 (A), R43.2
unnamed: D5.2 (A), R44.2
unnamed: R2.2, R3.1
unnamed: R1.2, R2.1, U12.94 (BOOT0)
unnamed: C17.1, U12.8 (PC14), Y3.1
unnamed: C16.2, U12.9 (PC15), Y3.2
unnamed: R44.1, U12.62 (PD15)
unnamed: C19.1, U12.13 (PH1), Y1.3 (CRYSTAL_2)
OE_PIN: U12.68 (PA9); also elsewhere on the board
OE_PIN2: U12.69 (PA10); also elsewhere on the board
SWCLK_Pin: U12.76 (PA14); also elsewhere on the board
SWDIO_Pin: U12.72 (PA13); also elsewhere on the board
Signal1_Pin: R42.1, TP12.1, U12.29 (PA4); also elsewhere on the board
Signal2_Pin: R43.1, TP13.1, U12.41 (PE10); also elsewhere on the board
TPS_ADC_SIGNAL: U12.15 (PC0); also elsewhere on the board

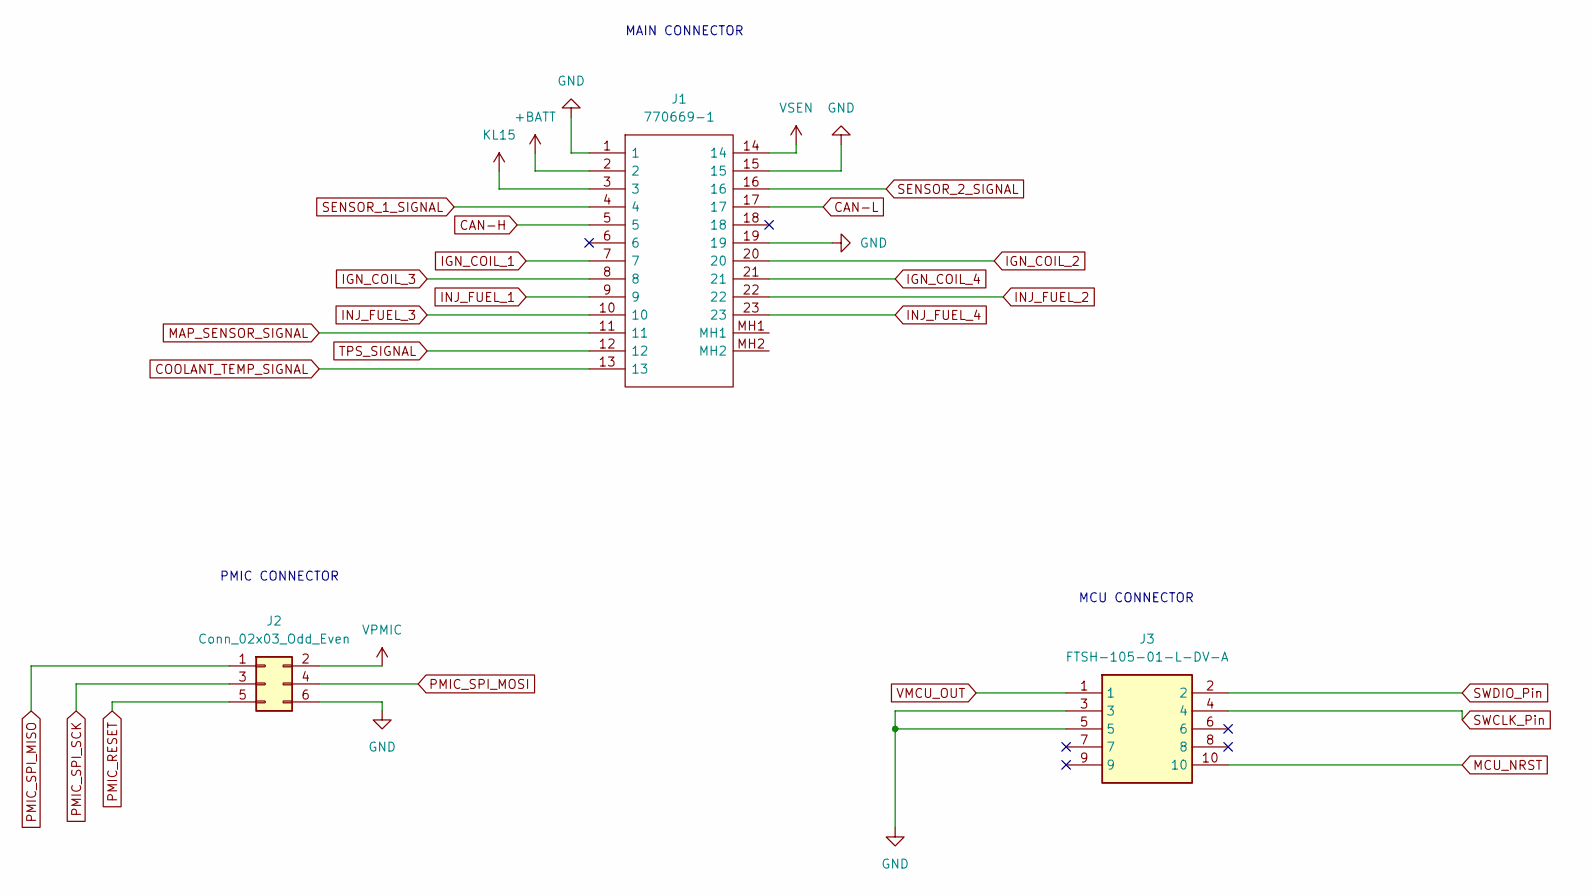
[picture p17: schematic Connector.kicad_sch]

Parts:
J1: 770669-1; 7706691; Mouser Part Number 571-770669-1
J2: Conn_02x03_Odd_Even; IDC-Header_2x03_P2.54mm_Vertical
J3: FTSH-105-01-L-DV-A; FTSH-105-XX-YYY-DV-A; Mouser Part Number 200-FTSH10501LDVA

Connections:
+BATT: J1.2; also elsewhere on the board
CAN-H: J1.5; also elsewhere on the board
CAN-L: J1.17; also elsewhere on the board
COOLANT_TEMP_ADC_SIGNAL: J1.13; also elsewhere on the board
IGN_COIL_1: J1.7; also elsewhere on the board
IGN_COIL_2: J1.20; also elsewhere on the board
IGN_COIL_3: J1.8; also elsewhere on the board
IGN_COIL_4: J1.21; also elsewhere on the board
INJ_FUEL_1: J1.9; also elsewhere on the board
INJ_FUEL_2: J1.22; also elsewhere on the board
INJ_FUEL_3: J1.10; also elsewhere on the board
INJ_FUEL_4: J1.23; also elsewhere on the board
MAP_SENSOR_SIGNAL: J1.11; also elsewhere on the board
MCU_NRST: J3.10; also elsewhere on the board
PMIC_RESET: J2.5; also elsewhere on the board
PMIC_SPI_MISO: J2.1; also elsewhere on the board
PMIC_SPI_MOSI: J2.4; also elsewhere on the board
PMIC_SPI_SCK: J2.3; also elsewhere on the board
SENSOR_1_SIGNAL: J1.4; also elsewhere on the board
SENSOR_2_SIGNAL: J1.16; also elsewhere on the board
SWCLK_Pin: J3.4; also elsewhere on the board
SWDIO_Pin: J3.2; also elsewhere on the board
TPS_SIGNAL: J1.12; also elsewhere on the board
VPMIC: J2.2; also elsewhere on the board
VSEN: J1.14; also elsewhere on the board

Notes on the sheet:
MCU CONNECTOR
MAIN CONNECTOR
PMIC CONNECTOR

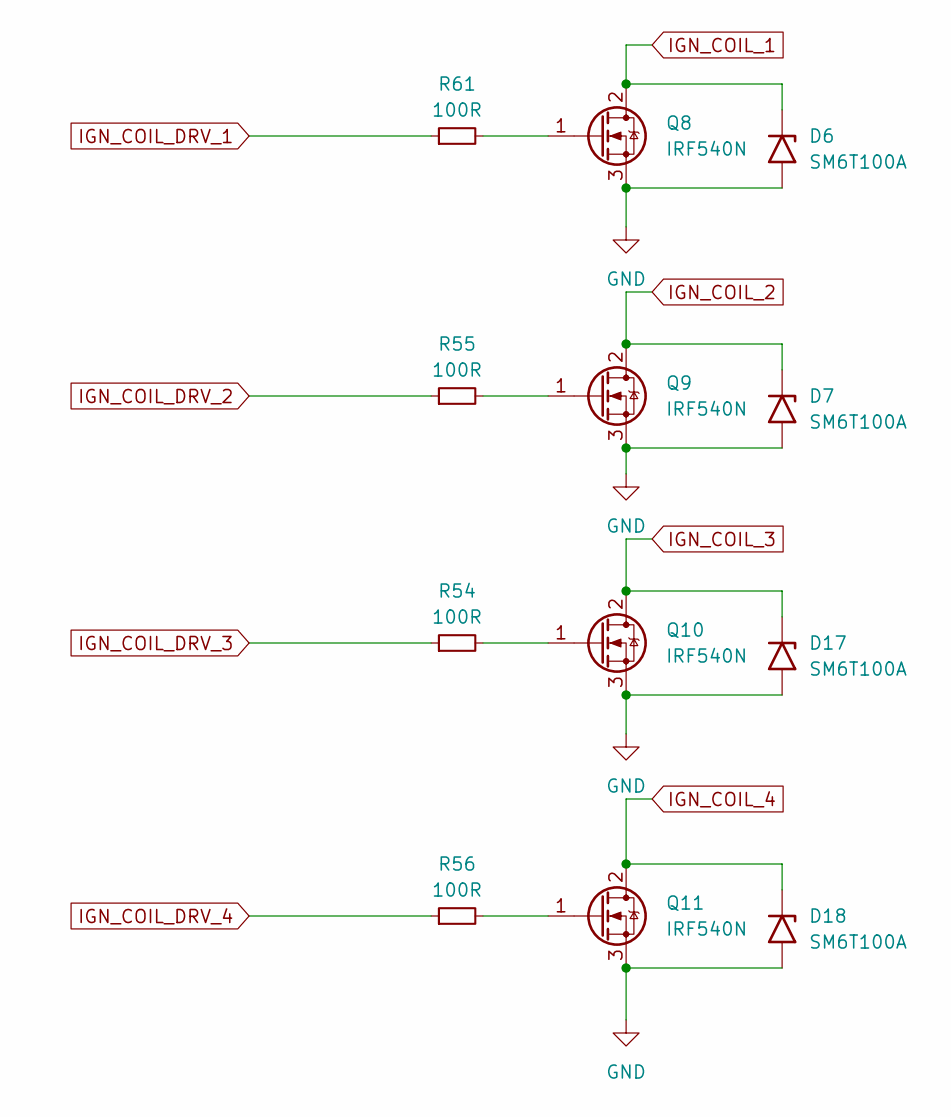
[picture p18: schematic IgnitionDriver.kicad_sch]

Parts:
D6, D7, D17, D18: SM6T100A; D_SMB
Q8, Q9, Q10, Q11: IRF540N; TO-220-3_Vertical
R54, R55, R56, R61: 100R; R_0603_1608Metric_Pad0.98x0.95mm_HandSolder

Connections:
IGN_COIL_1: D6.1 (A1), Q8.2 (D); also elsewhere on the board
IGN_COIL_2: D7.1 (A1), Q9.2 (D); also elsewhere on the board
IGN_COIL_3: D17.1 (A1), Q10.2 (D); also elsewhere on the board
IGN_COIL_4: D18.1 (A1), Q11.2 (D); also elsewhere on the board
IGN_COIL_DRV_1: R61.1; also elsewhere on the board
IGN_COIL_DRV_2: R55.1; also elsewhere on the board
IGN_COIL_DRV_3: R54.1; also elsewhere on the board
IGN_COIL_DRV_4: R56.1; also elsewhere on the board
unnamed: Q8.1 (G), R61.2
unnamed: Q9.1 (G), R55.2
unnamed: Q10.1 (G), R54.2
unnamed: Q11.1 (G), R56.2

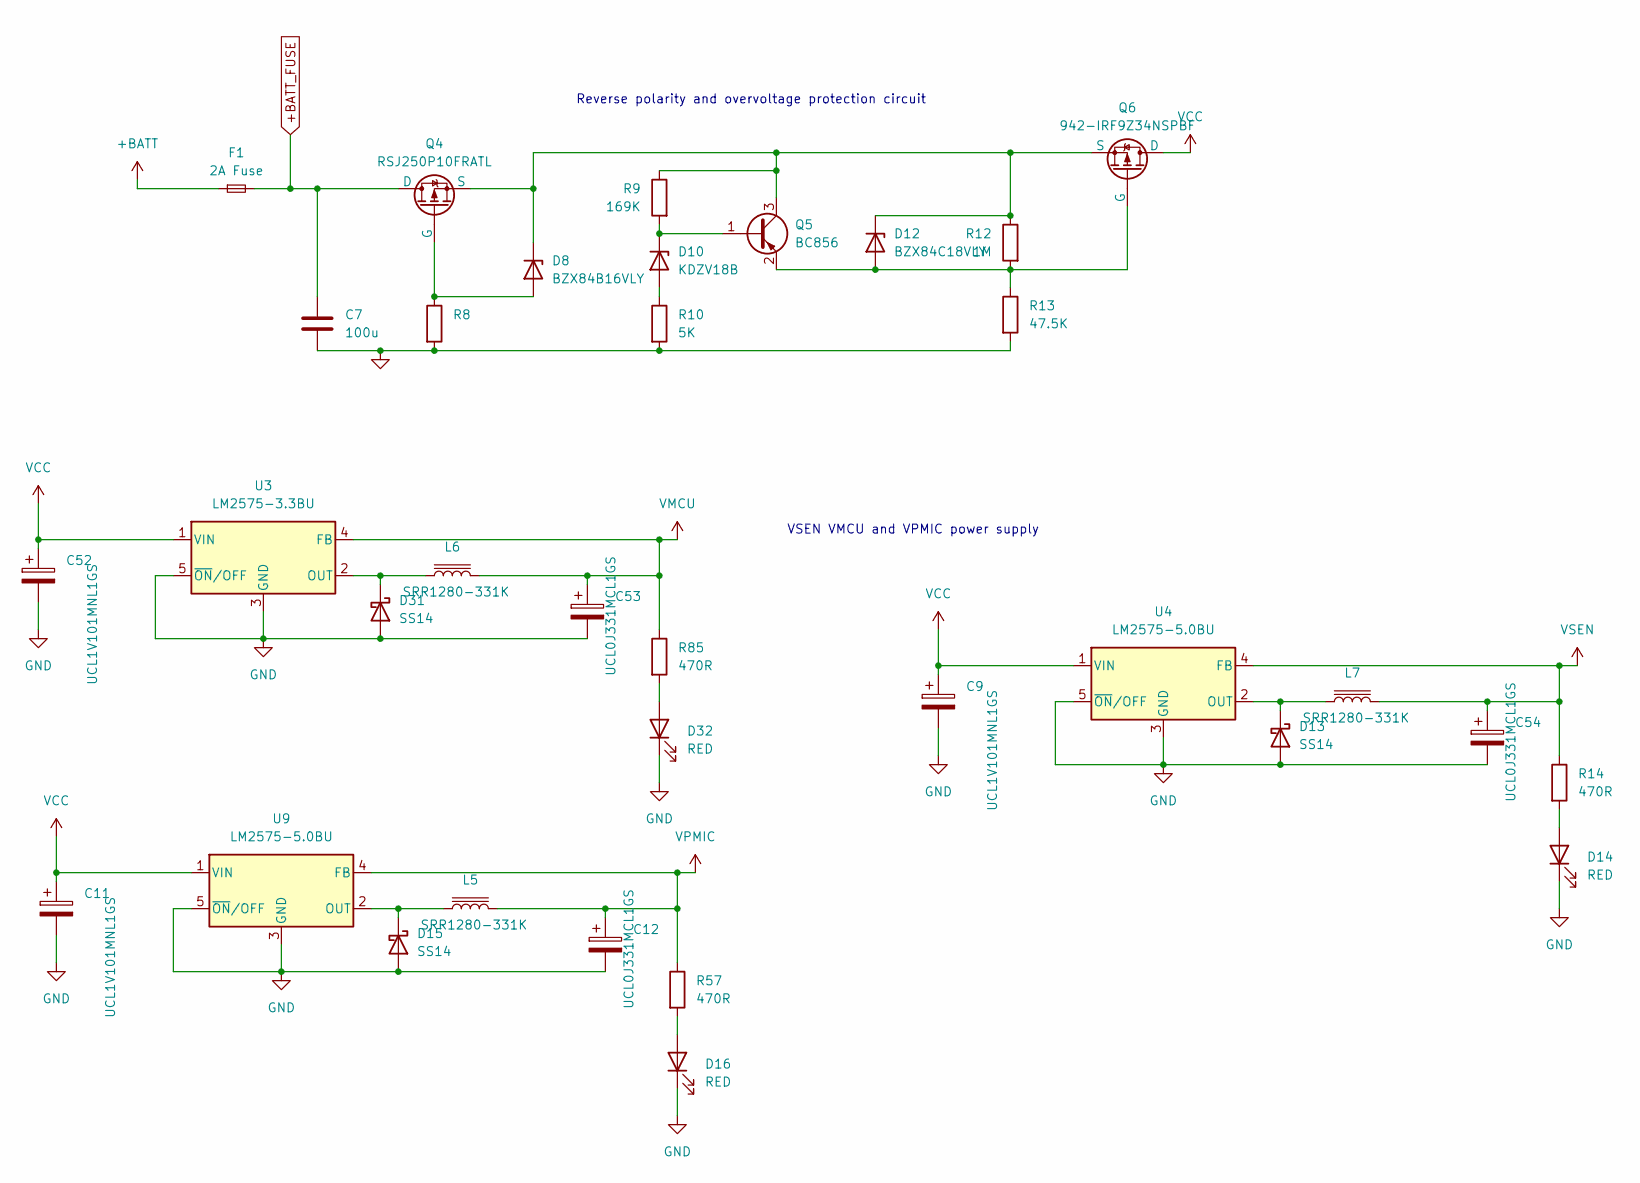
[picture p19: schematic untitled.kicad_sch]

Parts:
C7: 100u; C_0603_1608Metric_Pad1.08x0.95mm_HandSolder
C9, C52: UCL1V101MNL1GS; CP_Elec_8x11.9
C11: UCL1V101MNL1GS; CP_Elec_8x11.9; Mouser PN 647-UCL1V101MNL1GS
C12, C53, C54: UCL0J331MCL1GS; CP_Elec_6.3x7.7; Mouser PN 647-UCL0J331MCL1GS
D8: BZX84B16VLY; SOT-23
D10: KDZV18B; D_SOD-123
D12: BZX84C18VLY; SOT-23
D13, D31: SS14; D_SMA
D14, D16, D32: RED; LED_0805_2012Metric_Pad1.15x1.40mm_HandSolder
D15: SS14; D_SMA; Mouser PN 512-SS14
F1: 2A Fuse; Fuse_0805_2012Metric_Pad1.15x1.40mm_HandSolder
L5, L6, L7: SRR1280-331K; L_Bourns_SRR1260; Mouser PN 652-SRR1280-331K
Q4: RSJ250P10FRATL; TO-263-2_Transistor; Mouser PN 755-RSJ250P10FRATL
Q5: BC856; SOT-23
Q6: 942-IRF9Z34NSPBF; TO-263-2_Transistor
R8: 10K; R_0603_1608Metric_Pad0.98x0.95mm_HandSolder
R9: 169K; R_0603_1608Metric_Pad0.98x0.95mm_HandSolder
R10: 5K; R_0603_1608Metric_Pad0.98x0.95mm_HandSolder
R12: 1M; R_0603_1608Metric_Pad0.98x0.95mm_HandSolder
R13: 47.5K; R_0603_1608Metric_Pad0.98x0.95mm_HandSolder
R14, R57, R85: 470R; R_0603_1608Metric_Pad0.98x0.95mm_HandSolder
U3: LM2575-3.3BU; TO-263-5_TabPin3
U4: LM2575-5.0BU; TO-263-5_TabPin3
U9: LM2575-5.0BU; TO-263-5_TabPin3; Mouser PN 998-LM2575-5.0WU

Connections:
+BATT: F1.1; also elsewhere on the board
unnamed: D8.1 (A), Q4.1 (G), R8.1
unnamed: D10.2 (A), R10.1
unnamed: D10.1 (K), Q5.1 (B), R9.2
unnamed: D12.1 (A), Q5.2 (E), Q6.1 (G), R12.2, R13.1
unnamed: D8.3 (K), D12.3 (K), Q4.3 (S), Q5.3 (C), Q6.3 (S), R9.1, R12.1
unnamed: D13.1 (K), L7.1, U4.2 (OUT)
unnamed: D14.2 (A), R14.2
unnamed: D15.1 (K), L5.1, U9.2 (OUT)
unnamed: D16.2 (A), R57.2
unnamed: D31.1 (K), L6.1, U3.2 (OUT)
unnamed: D32.2 (A), R85.2
VCC: C9.1, C11.1, C52.1, Q6.2 (D), U3.1 (VIN), U4.1 (VIN), U9.1 (VIN)
VPMIC: C12.1, L5.2, R57.1, U9.4 (FB); also elsewhere on the board
VSEN: C54.1, L7.2, R14.1, U4.4 (FB); also elsewhere on the board

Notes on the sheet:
VSEN VMCU and VPMIC power supply
Reverse polarity and overvoltage protection circuit

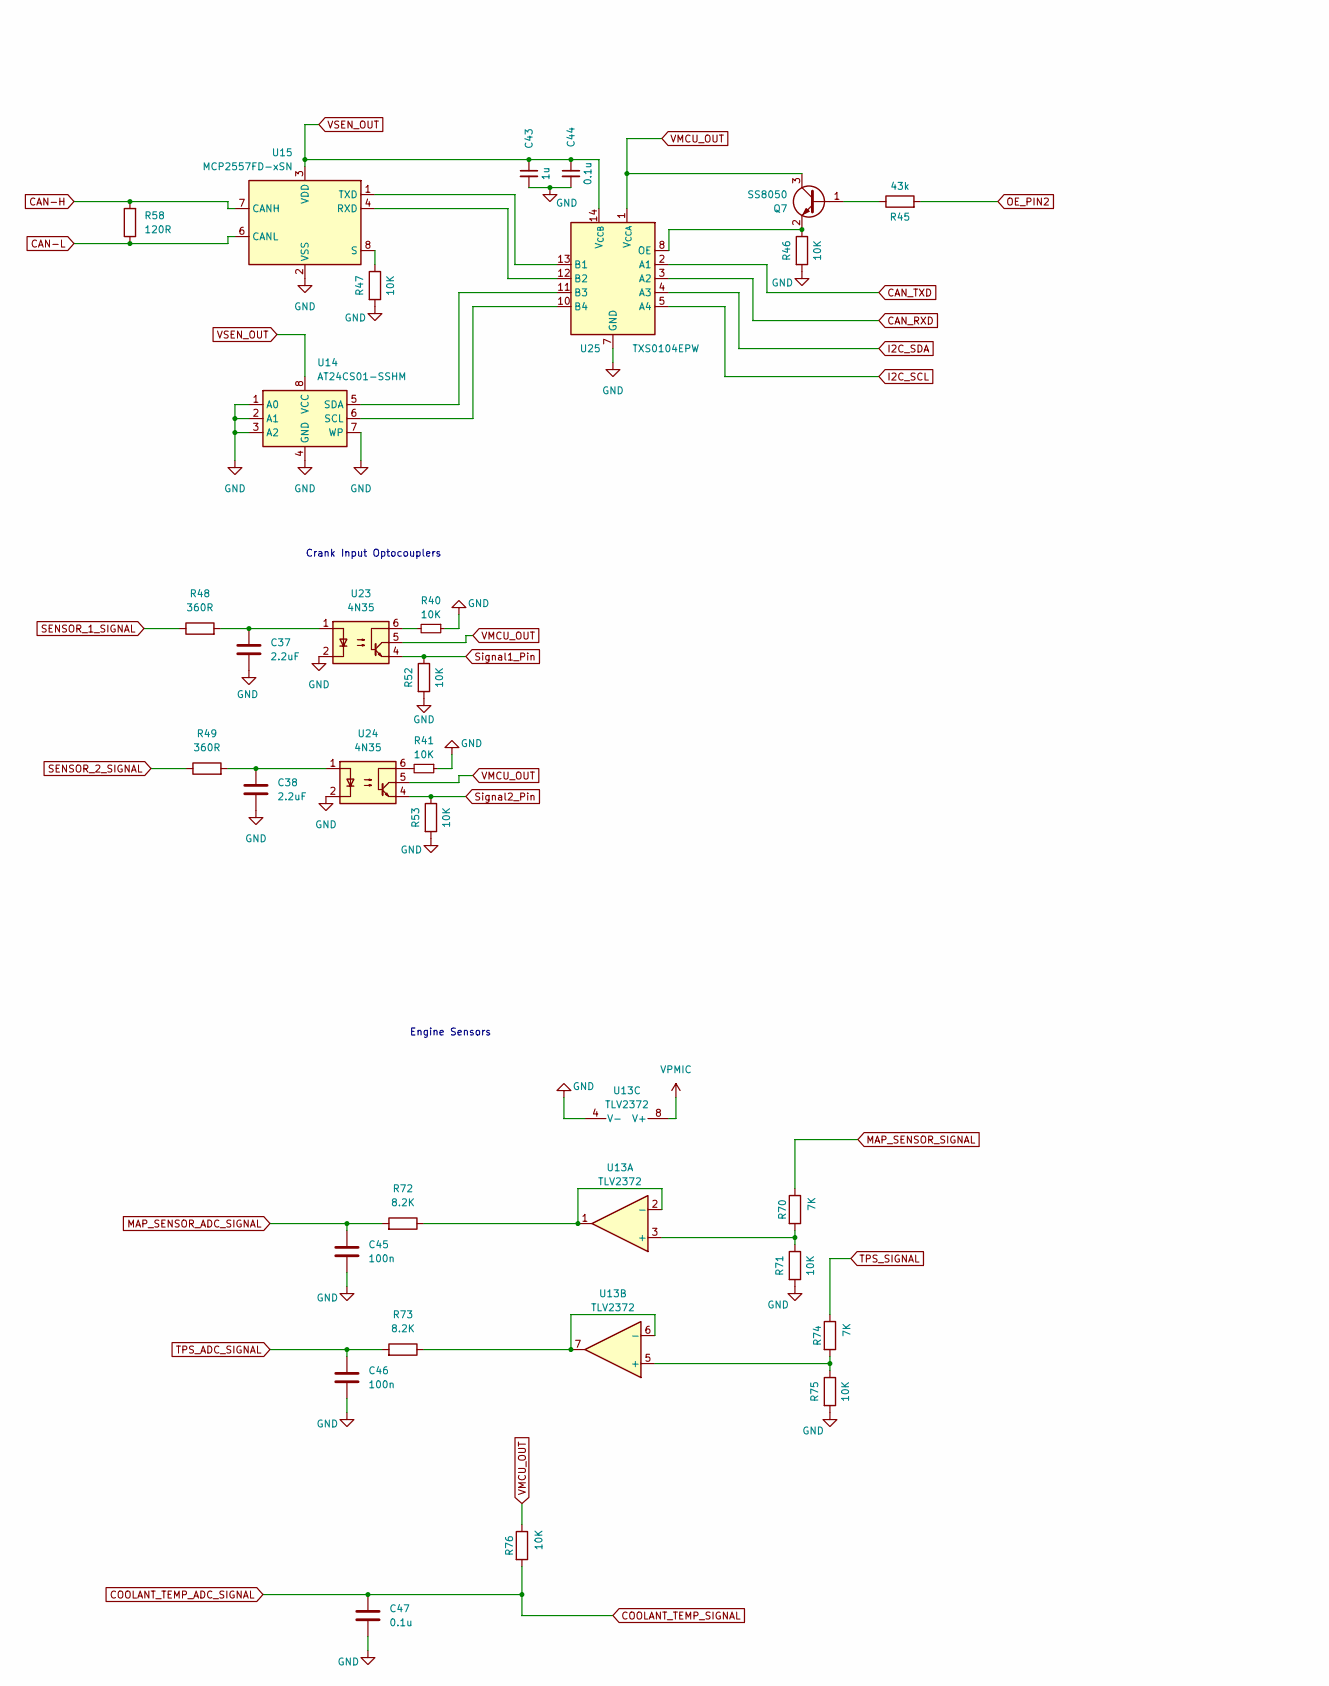
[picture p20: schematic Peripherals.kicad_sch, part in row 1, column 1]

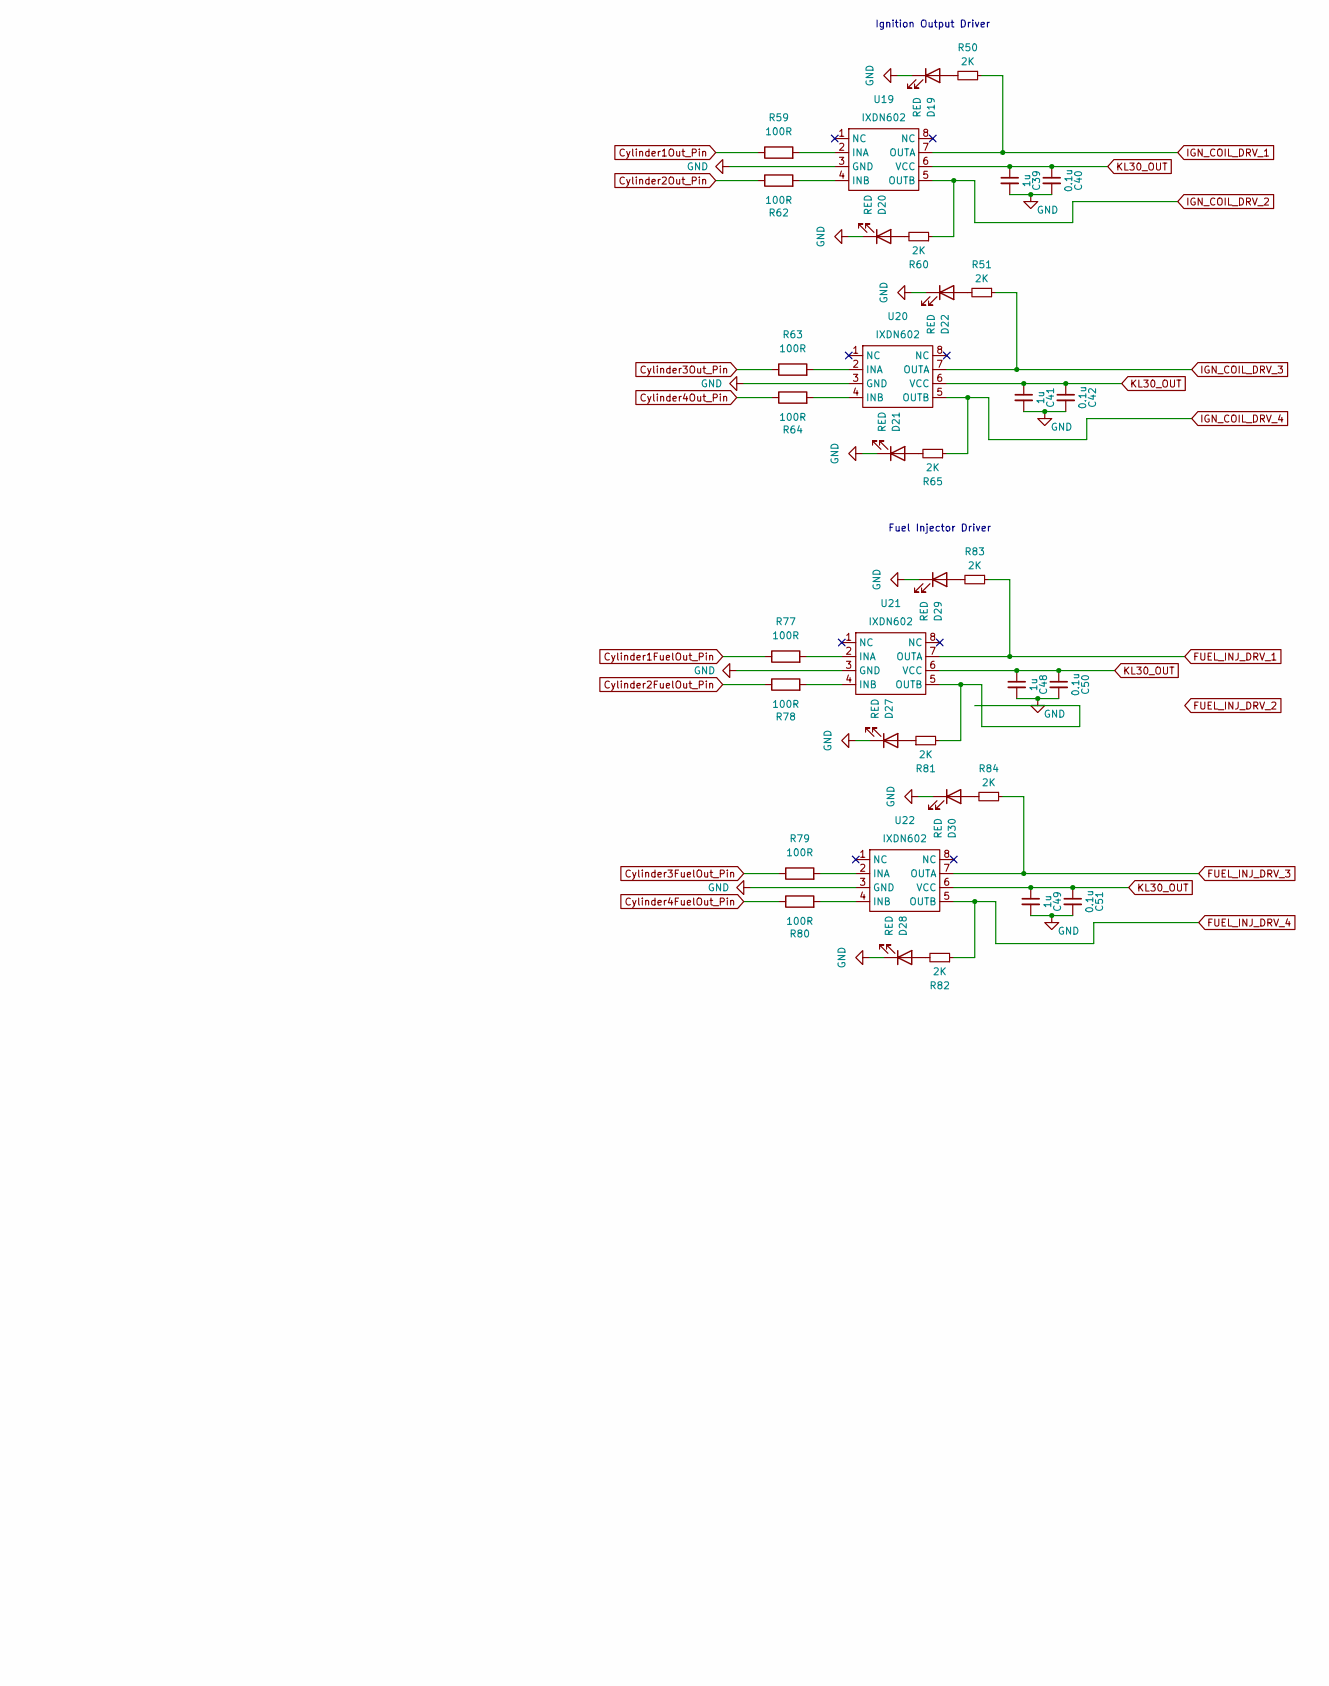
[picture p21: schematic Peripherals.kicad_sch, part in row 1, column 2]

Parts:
C37, C38: 2.2uF; C_0603_1608Metric_Pad1.08x0.95mm_HandSolder
C39, C41, C43, C48, C49: 1u; C_0603_1608Metric_Pad1.08x0.95mm_HandSolder
C40, C42, C44, C47, C50, C51: 0.1u; C_0603_1608Metric_Pad1.08x0.95mm_HandSolder
C45, C46: 100n; C_0603_1608Metric_Pad1.08x0.95mm_HandSolder
D19, D20, D21, D22, D27, D28, D29, D30: RED; LED_1206_3216Metric_Pad1.42x1.75mm_HandSolder
Q7: SS8050; TSOT-23_HandSoldering
R40, R41, R46, R47, R52, R53, R71, R75, R76: 10K; R_0603_1608Metric_Pad0.98x0.95mm_HandSolder
R45: 43k; R_0603_1608Metric_Pad0.98x0.95mm_HandSolder
R48, R49: 360R; R_0603_1608Metric_Pad0.98x0.95mm_HandSolder
R50, R51, R60, R65, R81, R82, R83, R84: 2K; R_0603_1608Metric_Pad0.98x0.95mm_HandSolder
R58: 120R; R_0603_1608Metric_Pad0.98x0.95mm_HandSolder
R59, R62, R63, R64, R77, R78, R79, R80: 100R; R_0603_1608Metric_Pad0.98x0.95mm_HandSolder
R70, R74: 7K; R_0603_1608Metric_Pad0.98x0.95mm_HandSolder
R72, R73: 8.2K; R_0603_1608Metric_Pad0.98x0.95mm_HandSolder
U13: TLV2372; SOIC-8_5.3x6.2mm_P1.27mm
U14: AT24CS01-SSHM; SOIC-8_3.9x4.9mm_P1.27mm
U15: MCP2557FD-xSN; SOIC-8_3.9x4.9mm_P1.27mm
U19, U20, U21, U22: IXDN602; SO-8_3.9x4.9mm_P1.27mm
U23, U24: 4N35; 4N35S
U25: TXS0104EPW; TSSOP-14_4.4x5mm_P0.65mm

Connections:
CAN-H: R58.2, U15.7 (CANH); also elsewhere on the board
CAN-L: R58.1, U15.6 (CANL); also elsewhere on the board
CAN_RXD: U25.3 (A2); also elsewhere on the board
CAN_TXD: U25.2 (A1); also elsewhere on the board
COOLANT_TEMP_ADC_SIGNAL: C47.1, R76.2; also elsewhere on the board
Cylinder1FuelOut_Pin: R77.1; also elsewhere on the board
Cylinder1Out_Pin: R59.1; also elsewhere on the board
Cylinder2FuelOut_Pin: R78.1; also elsewhere on the board
Cylinder2Out_Pin: R62.1; also elsewhere on the board
Cylinder3FuelOut_Pin: R79.1; also elsewhere on the board
Cylinder3Out_Pin: R63.1; also elsewhere on the board
Cylinder4FuelOut_Pin: R80.1; also elsewhere on the board
Cylinder4Out_Pin: R64.1; also elsewhere on the board
FUEL_INJ_DRV_1: R83.1, U21.7 (OUTA); also elsewhere on the board
FUEL_INJ_DRV_3: R84.1, U22.7 (OUTA); also elsewhere on the board
FUEL_INJ_DRV_4: R82.1, U22.5 (OUTB); also elsewhere on the board
I2C_SCL: U25.5 (A4); also elsewhere on the board
I2C_SDA: U25.4 (A3); also elsewhere on the board
IGN_COIL_DRV_1: R50.1, U19.7 (OUTA); also elsewhere on the board
IGN_COIL_DRV_2: R60.1, U19.5 (OUTB); also elsewhere on the board
IGN_COIL_DRV_3: R51.1, U20.7 (OUTA); also elsewhere on the board
IGN_COIL_DRV_4: R65.1, U20.5 (OUTB); also elsewhere on the board
KL30_OUT: C39.1, C40.1, C41.1, C42.1, C48.1, C49.1, C50.1, C51.1, U19.6 (VCC), U20.6 (VCC), U21.6 (VCC), U22.6 (VCC); also elsewhere on the board
MAP_SENSOR_ADC_SIGNAL: C45.1, R72.2; also elsewhere on the board
MAP_SENSOR_SIGNAL: R70.1; also elsewhere on the board
unnamed: C37.1, R48.2, U23.1
unnamed: C38.1, R49.2, U24.1
unnamed: D19.2 (A), R50.2
unnamed: D20.2 (A), R60.2
unnamed: D21.2 (A), R65.2
unnamed: D22.2 (A), R51.2
unnamed: D27.2 (A), R81.1
unnamed: D28.2 (A), R82.2
unnamed: D29.2 (A), R83.2
unnamed: D30.2 (A), R84.2
unnamed: Q7.1 (B), R45.1
unnamed: Q7.2 (E), R46.1, U25.8 (OE)
unnamed: R40.2, U23.6
unnamed: R41.2, U24.6
unnamed: R70.2, R71.1, U13.3 (+)
unnamed: R72.1, U13.1, U13.2 (-)
unnamed: R74.2, R75.1, U13.5 (+)
unnamed: R73.1, U13.6 (-), U13.7
unnamed: U14.6 (SCL), U25.10 (B4)
unnamed: U14.5 (SDA), U25.11 (B3)
unnamed: U15.4 (RXD), U25.12 (B2)
unnamed: R47.1, U15.8 (S)
unnamed: U15.1 (TXD), U25.13 (B1)
unnamed: R59.2, U19.2 (INA)
unnamed: R62.2, U19.4 (INB)
unnamed: R63.2, U20.2 (INA)
unnamed: R64.2, U20.4 (INB)
unnamed: R77.2, U21.2 (INA)
unnamed: R78.2, U21.4 (INB)
unnamed: R81.2, U21.5 (OUTB)
unnamed: R79.2, U22.2 (INA)
unnamed: R80.2, U22.4 (INB)
OE_PIN2: R45.2; also elsewhere on the board
SENSOR_1_SIGNAL: R48.1; also elsewhere on the board
SENSOR_2_SIGNAL: R49.1; also elsewhere on the board
Signal1_Pin: R52.1, U23.4; also elsewhere on the board
Signal2_Pin: R53.1, U24.4; also elsewhere on the board
TPS_ADC_SIGNAL: C46.1, R73.2; also elsewhere on the board
TPS_SIGNAL: R74.1; also elsewhere on the board
VPMIC: U13.8 (V+); also elsewhere on the board
VSEN_OUT: C43.1, C44.1, U14.8 (VCC), U15.3 (VDD), U25.14 (V_{CCB}); also elsewhere on the board

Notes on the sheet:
Crank Input Optocouplers
Fuel Injector Driver
Engine Sensors
Ignition Output Driver

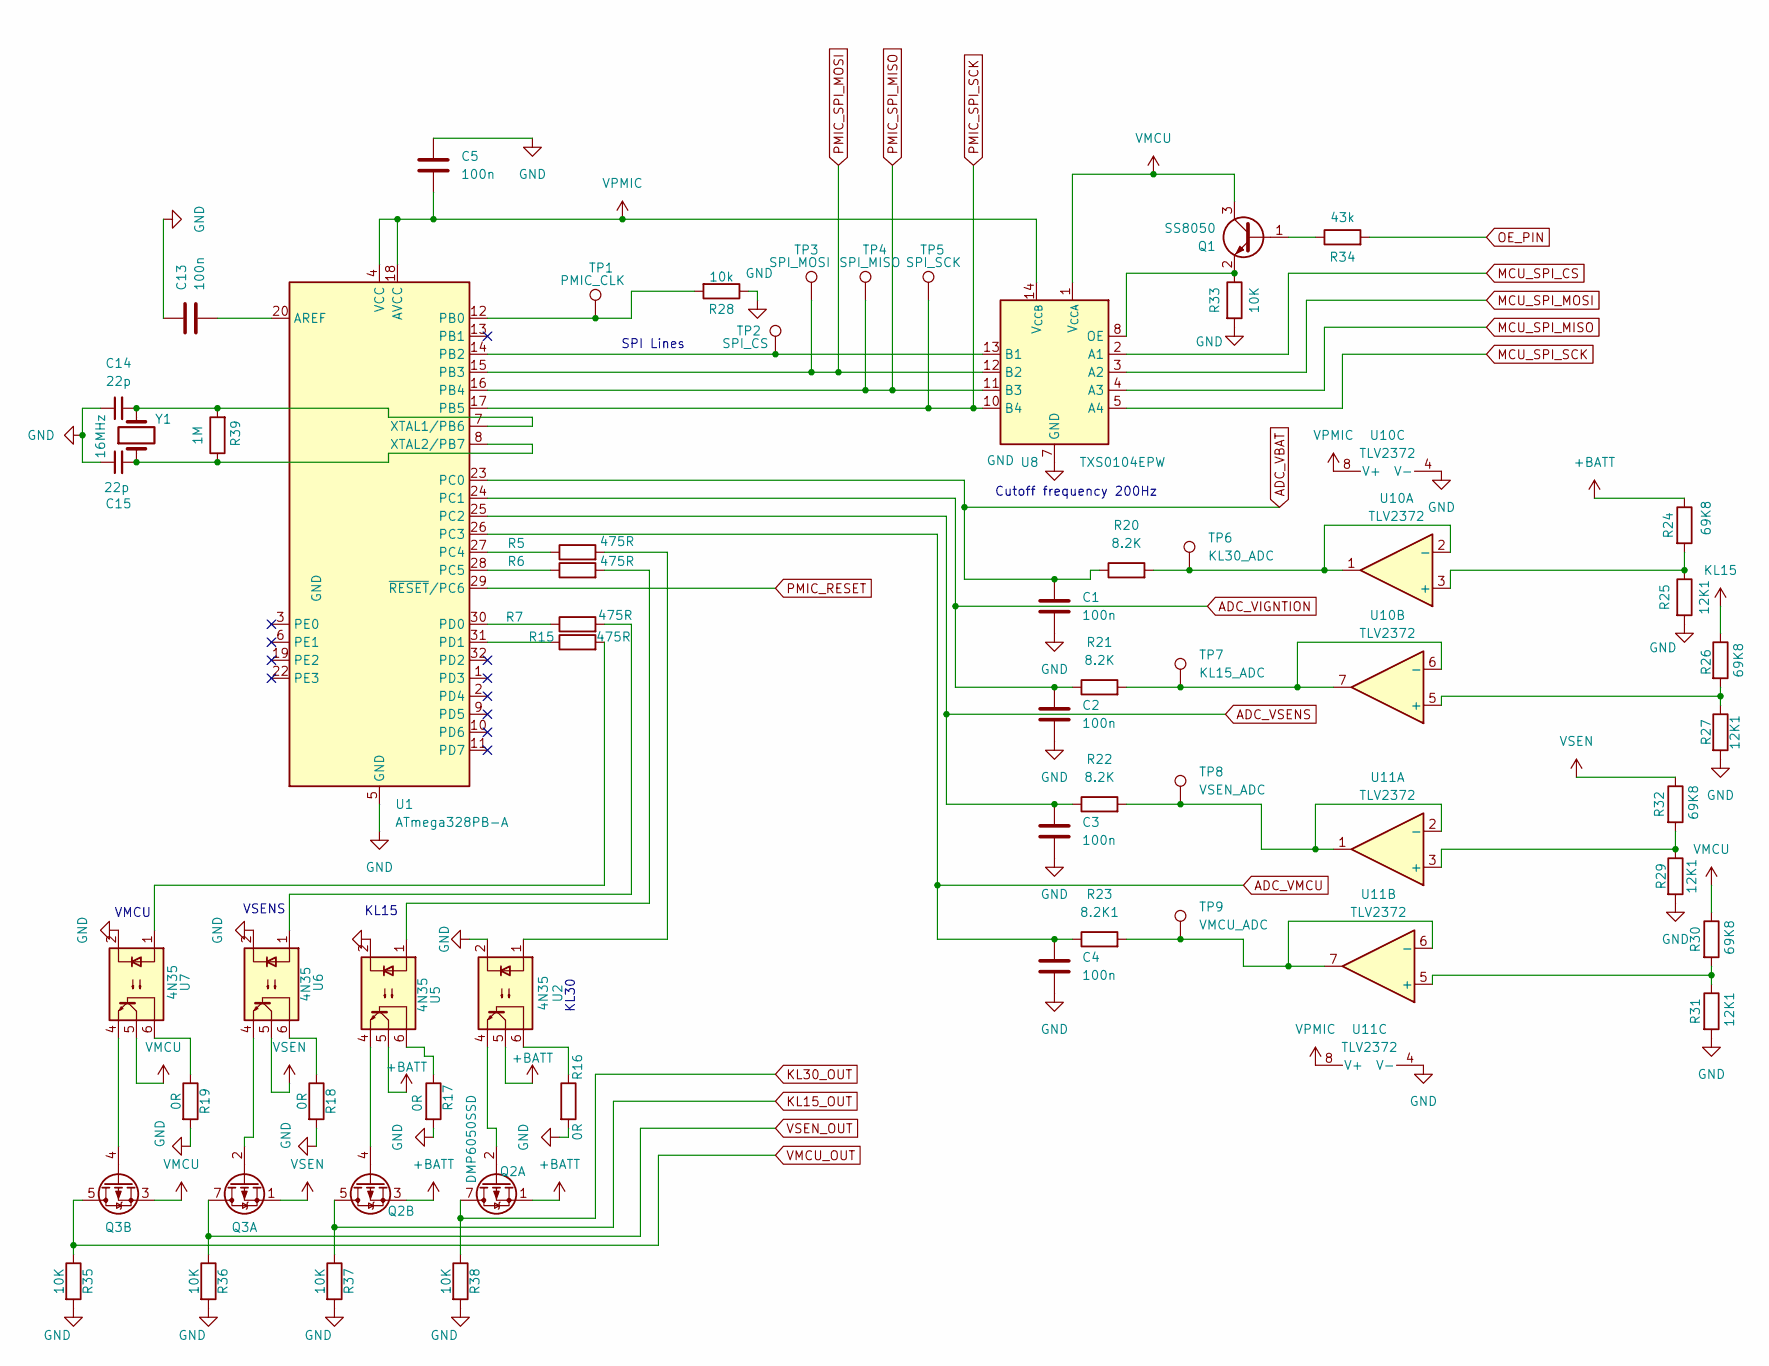
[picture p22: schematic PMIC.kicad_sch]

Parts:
C1, C2, C3, C4, C5, C13: 100n; C_0603_1608Metric_Pad1.08x0.95mm_HandSolder
C14, C15: 22p; C_0603_1608Metric_Pad1.08x0.95mm_HandSolder
Q1: SS8050; TSOT-23_HandSoldering
Q2, Q3: DMP6050SSD; SOIC-8_3.9x4.9mm_P1.27mm
R5, R6, R7, R15: 475R; R_0603_1608Metric_Pad0.98x0.95mm_HandSolder
R16, R17, R18, R19: 0R; R_0603_1608Metric_Pad0.98x0.95mm_HandSolder
R20, R21, R22: 8.2K; R_0603_1608Metric_Pad0.98x0.95mm_HandSolder
R23: 8.2K1; R_0603_1608Metric_Pad0.98x0.95mm_HandSolder
R24, R26, R30, R32: 69K8; R_0603_1608Metric_Pad0.98x0.95mm_HandSolder
R25, R27, R29, R31: 12K1; R_0603_1608Metric_Pad0.98x0.95mm_HandSolder
R28: 10k; R_0603_1608Metric_Pad0.98x0.95mm_HandSolder
R33, R35, R36, R37, R38: 10K; R_0603_1608Metric_Pad0.98x0.95mm_HandSolder
R34: 43k; R_0603_1608Metric_Pad0.98x0.95mm_HandSolder
R39: 1M; R_0603_1608Metric_Pad0.98x0.95mm_HandSolder
TP1: PMIC_CLK; TestPoint_Pad_1.0x1.0mm
TP2: SPI_CS; TestPoint_Pad_1.0x1.0mm
TP3: SPI_MOSI; TestPoint_Pad_1.0x1.0mm
TP4: SPI_MISO; TestPoint_Pad_1.0x1.0mm
TP5: SPI_SCK; TestPoint_Pad_1.0x1.0mm
TP6: KL30_ADC; TestPoint_Pad_1.0x1.0mm
TP7: KL15_ADC; TestPoint_Pad_1.0x1.0mm
TP8: VSEN_ADC; TestPoint_Pad_1.0x1.0mm
TP9: VMCU_ADC; TestPoint_Pad_1.0x1.0mm
U1: ATmega328PB-A; TQFP-32_7x7mm_P0.8mm
U2, U5, U6, U7: 4N35; 4N35S
U8: TXS0104EPW; TSSOP-14_4.4x5mm_P0.65mm
U10, U11: TLV2372; SOIC-8_5.3x6.2mm_P1.27mm
Y1: 16MHz; Crystal_HC52-8mm_Horizontal

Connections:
ADC_VBAT: C1.1, R20.1, U1.23 (PC0); also elsewhere on the board
ADC_VIGNTION: C2.1, R21.1, U1.24 (PC1); also elsewhere on the board
ADC_VMCU: C4.1, R23.1, U1.26 (PC3); also elsewhere on the board
ADC_VSENS: C3.1, R22.1, U1.25 (PC2); also elsewhere on the board
KL15_OUT: Q2.5 (D2), Q2.6 (D2), R37.1
KL30_OUT: Q2.7 (D1), Q2.8 (D1), R38.1; also elsewhere on the board
MCU_SPI_CS: U8.2 (A1); also elsewhere on the board
MCU_SPI_MISO: U8.4 (A3); also elsewhere on the board
MCU_SPI_MOSI: U8.3 (A2); also elsewhere on the board
MCU_SPI_SCK: U8.5 (A4); also elsewhere on the board
unnamed: Q1.1 (B), R34.1
unnamed: Q1.2 (E), R33.1, U8.8 (OE)
unnamed: Q2.2 (G1), U2.4
unnamed: Q2.4 (G2), U5.4
unnamed: Q3.2 (G1), U6.4
unnamed: Q3.4 (G2), U7.4
unnamed: R5.2, U2.1
unnamed: R6.2, U5.1
unnamed: R7.2, U6.1
unnamed: R15.2, U7.1
unnamed: R16.1, U2.6
unnamed: R17.1, U5.6
unnamed: R18.1, U6.6
unnamed: R19.1, U7.6
unnamed: C13.2, U1.20 (AREF)
unnamed: R28.2, TP1.1, U1.12 (PB0)
unnamed: TP2.1, U1.14 (PB2), U8.13 (B1)
unnamed: R5.1, U1.27 (PC4)
unnamed: R6.1, U1.28 (PC5)
unnamed: R7.1, U1.30 (PD0)
unnamed: R15.1, U1.31 (PD1)
unnamed: R24.2, R25.1, U10.3 (+)
unnamed: R20.2, TP6.1, U10.1, U10.2 (-)
unnamed: R26.2, R27.1, U10.5 (+)
unnamed: R21.2, TP7.1, U10.6 (-), U10.7
unnamed: R29.1, R32.2, U11.3 (+)
unnamed: R22.2, TP8.1, U11.1, U11.2 (-)
unnamed: R30.2, R31.1, U11.5 (+)
unnamed: R23.2, TP9.1, U11.6 (-), U11.7
OE_PIN: R34.2; also elsewhere on the board
PMIC_RESET: U1.29 (~RESET/PC6); also elsewhere on the board
PMIC_SPI_MISO: TP4.1, U1.16 (PB4), U8.11 (B3); also elsewhere on the board
PMIC_SPI_MOSI: TP3.1, U1.15 (PB3), U8.12 (B2); also elsewhere on the board
PMIC_SPI_SCK: TP5.1, U1.17 (PB5), U8.10 (B4); also elsewhere on the board
VPMIC: C5.2, U1.4 (VCC), U1.18 (AVCC), U8.14 (V_{CCB}), U10.8 (V+), U11.8 (V+); also elsewhere on the board
VSEN: Q3.1 (S1), R32.1, U6.5; also elsewhere on the board
VSEN_OUT: Q3.7 (D1), Q3.8 (D1), R36.1; also elsewhere on the board

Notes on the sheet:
KL15
Cutoff frequency 200Hz
VMCU
KL30
SPI Lines
VSENS

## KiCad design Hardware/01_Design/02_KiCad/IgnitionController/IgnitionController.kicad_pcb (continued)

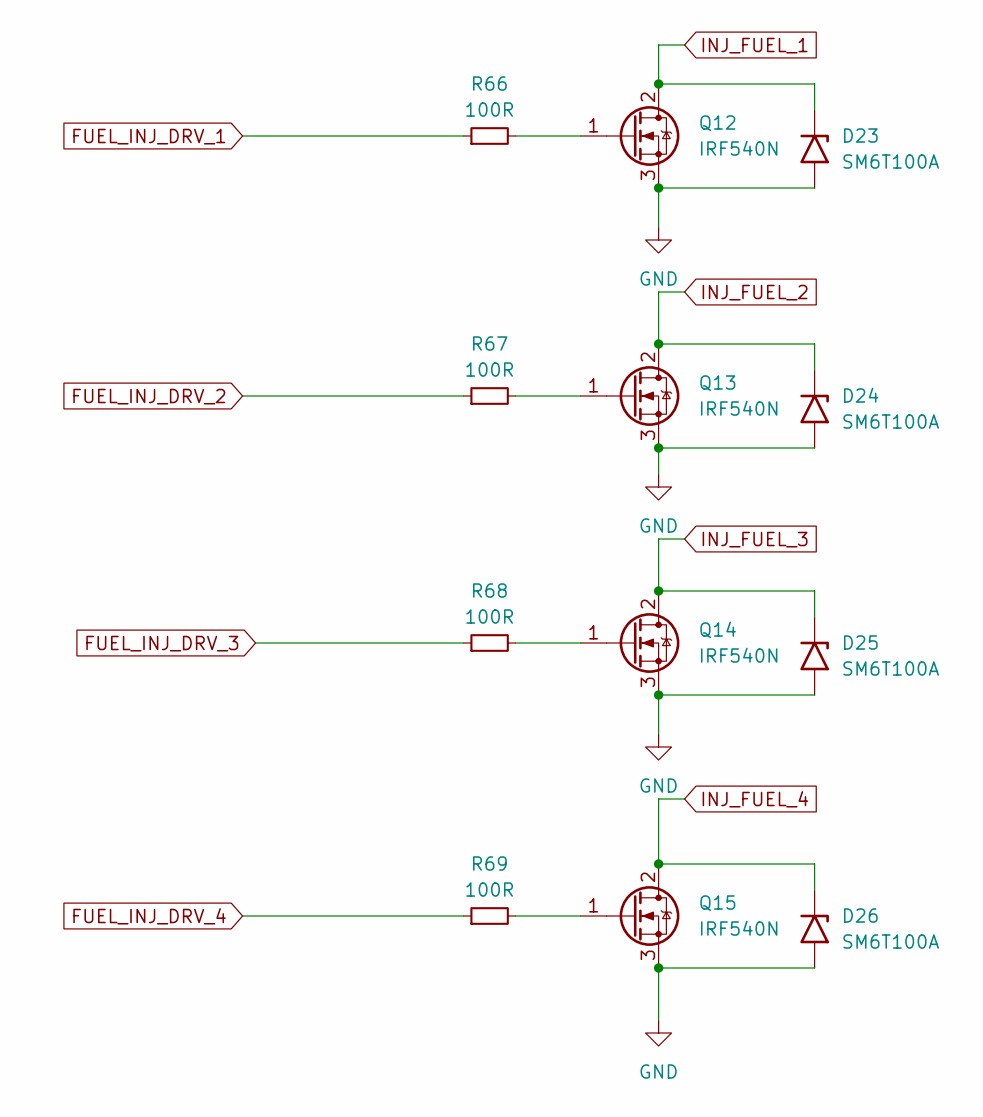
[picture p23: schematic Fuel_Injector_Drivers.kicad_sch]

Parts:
D23, D24, D25, D26: SM6T100A; D_SMB
Q12, Q13, Q14, Q15: IRF540N; TO-220-3_Vertical
R66, R67, R68, R69: 100R; R_0603_1608Metric_Pad0.98x0.95mm_HandSolder

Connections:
FUEL_INJ_DRV_1: R66.1; also elsewhere on the board
FUEL_INJ_DRV_2: R67.1
FUEL_INJ_DRV_3: R68.1; also elsewhere on the board
FUEL_INJ_DRV_4: R69.1; also elsewhere on the board
INJ_FUEL_1: D23.1 (A1), Q12.2 (D); also elsewhere on the board
INJ_FUEL_2: D24.1 (A1), Q13.2 (D); also elsewhere on the board
INJ_FUEL_3: D25.1 (A1), Q14.2 (D); also elsewhere on the board
INJ_FUEL_4: D26.1 (A1), Q15.2 (D); also elsewhere on the board
unnamed: Q12.1 (G), R66.2
unnamed: Q13.1 (G), R67.2
unnamed: Q14.1 (G), R68.2
unnamed: Q15.1 (G), R69.2

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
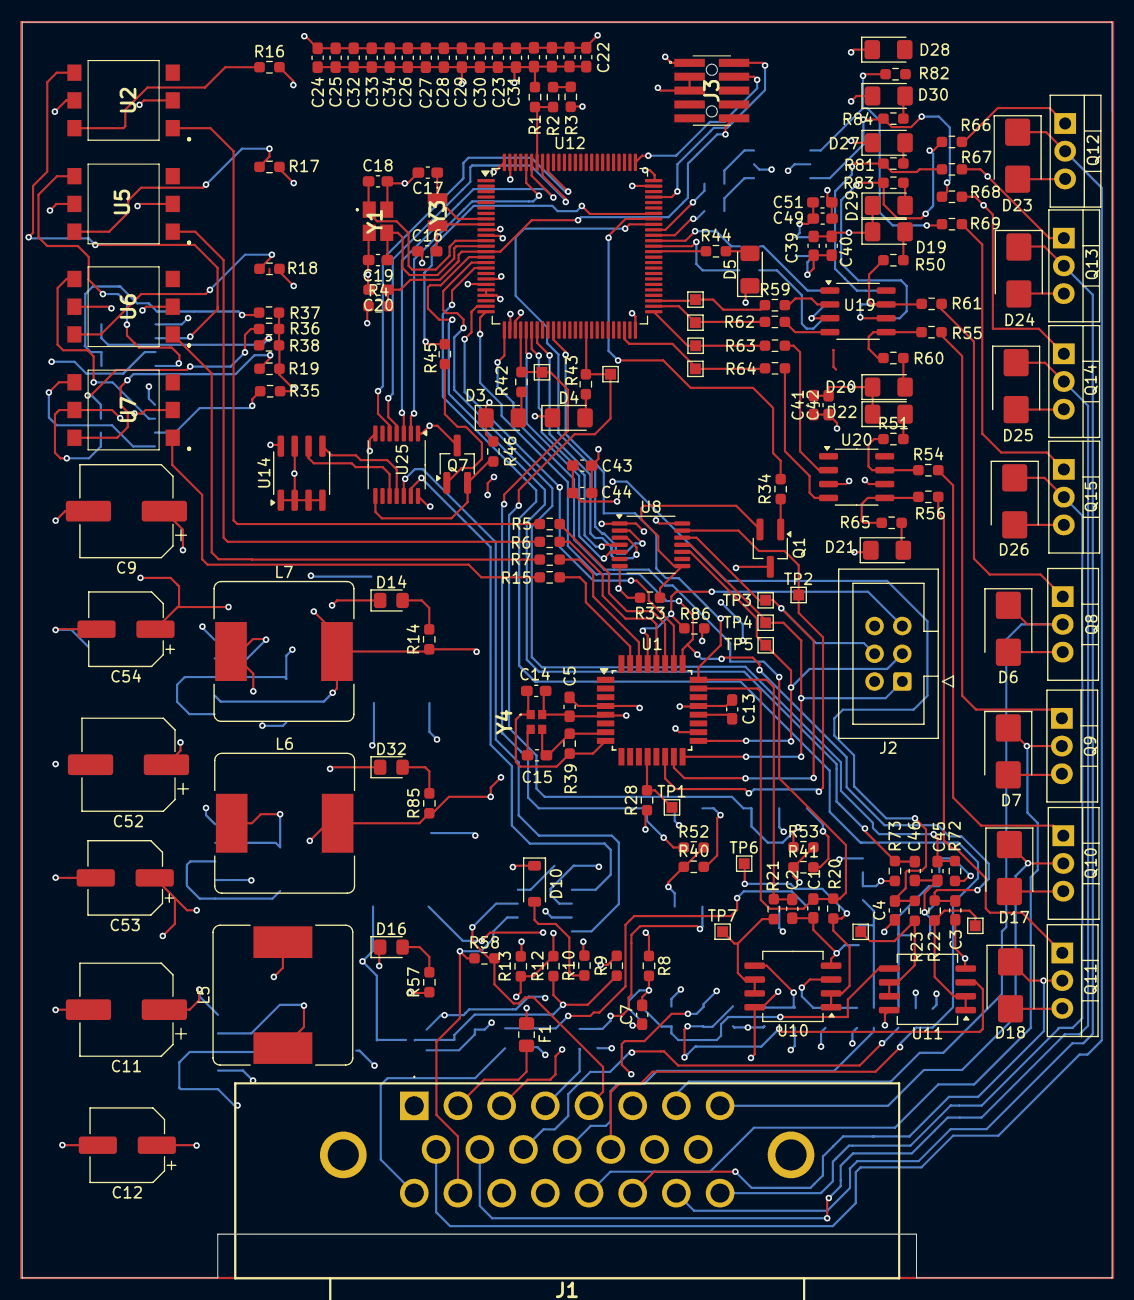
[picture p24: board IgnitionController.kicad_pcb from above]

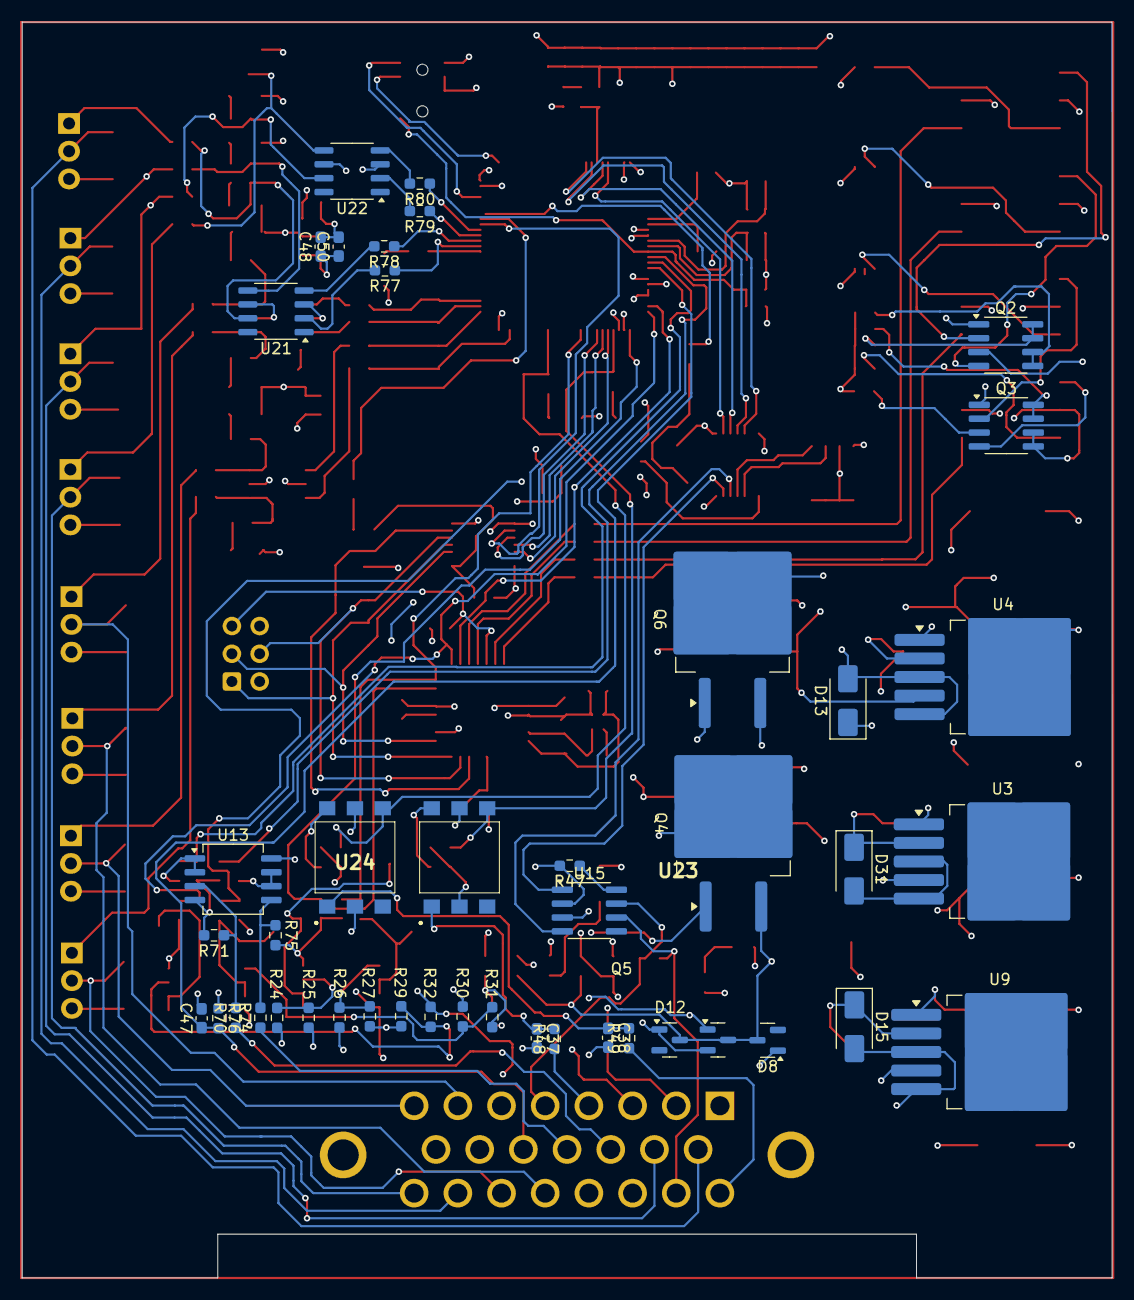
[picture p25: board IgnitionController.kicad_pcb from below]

Board: 4 copper layers, 99.8 x 115.0 mm, 226 parts (44 on the bottom side), 159 nets.

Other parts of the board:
R86: 10k; R_0603_1608Metric_Pad0.98x0.95mm_HandSolder
Y4: NX2016SA-16MHZ-EXS00A-CS07826; NX2016SA16MHZEXS00ACS07826

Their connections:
PMIC_RESET: R86.2; also elsewhere on the board
VPMIC: R86.1; also elsewhere on the board

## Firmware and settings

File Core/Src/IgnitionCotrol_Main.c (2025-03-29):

/**
 * @file      IgnitionCotrol_Main.c
 * @authors   Miroslav Mitrovic
 * Created on September 16, 2022, 7:33 PM
 * @Copyright 2022 by Miroslav Mitrovic <mmitrovicmas13@gmail.com>
 *
 * This file is part of open source application.
 * 
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
 * @license GPL-3.0+ <http://spdx.org/licenses/GPL-3.0+>
 *
 * @brief [description]
 *
 *******************************************************************************/
 
#include "IgnitionCotrol_Main.h"
//extern UART_HandleTypeDef huart2;
extern volatile uint32_t g_usSinceDetectionCyl1;
extern volatile uint32_t g_usSinceDetectionCyl2;
uint32_t g_FirstSensorTimePrevious_us = 0;
uint32_t g_FirstSensorTimeCurrent_us = 0;
uint32_t g_SecondSensorTimePrevious_us = 0;
uint32_t g_SecondSensorTimeCurrent_us = 0;
uint32_t g_SensorActivationCounter = 0;
uint32_t g_SensorActivationCounterCylinder2 = 0;
uint32_t g_LostSyncCounter = 0;
uint32_t g_FirstSensorTime_us = 0;
uint32_t g_SecondSensorTime_us = 0;
/*Flag with the signal status*/
uint8_t  g_SignalFlag = 0;
/*Signal state Flag*/
uint8_t g_SignalState = 0;
/*Flag with the sync status*/
uint8_t  g_SyncFlag = 0;
/*Flag for check if the sensor Value is already taken*/
uint8_t g_FirstSensorSignalAvailable = false;

/* First cylinder RPM rate of change variable */
static double g_RPMPrevTimeDifference_us = 0.0;
/* Second cylinder RPM rate of change variable */
static double g_RPM2PrevTimeDifference_us = 0.0;
/* Flag to handle the transition from cranking to firing */
uint8_t g_CrankingFiringFlag = 0U;
static double g_PrevTimeDifference_us = 0.0;
/*Handler for Calculation States*/
static void Calculation_v_Handler(void);
/*Handler for Firing States*/
static  void Firing_v_Handler(void);
/*Check for the first sensor is available, and if it is, it returns the status and 
 sets the time for first sensor*/
static uint8_t IgnitionControl_FirstSensorCheck(void);

/*Check for the second sensor is available, and if it is, it returns the status and 
 sets the time for first sensor*/
//static uint8_t IgnitionControl_SecondSensorCheck(void);
/*To check if the sensors are in sync*/
static uint8_t IgntionControl_SyncCheck(void);

/* returns calculated rate of change of in value*/
static uint32_t CalculateRate_u_OfChange(uint32_t *in_prevValue, uint32_t in_currValue )
{
    double l_DeltaTimeDifference_us = 0.0;
    l_DeltaTimeDifference_us = (in_currValue - *(in_prevValue) ) / 1.0;
    *in_prevValue = in_currValue;

    return in_currValue +=(uint32_t)l_DeltaTimeDifference_us;

}

uint32_t Calculate_u_Microseconds(uint32_t MicrosecondsTicks)
{
	return MicrosecondsTicks * 10; //Frequency is set @ 84MHz and prescaler is 10. Counter is 10->10uS per tick.
}

void IgnitionControl_v_Main(void)
{


    HAL_NVIC_DisableIRQ(EXTI4_IRQn);
	// Firing_v_Handler();
    Calculation_v_Handler();
    HAL_NVIC_EnableIRQ(EXTI4_IRQn);
     // HAL_GPIO_TogglePin(TestLED1_GPIO_Port,TestLED1_Pin);
    HAL_NVIC_DisableIRQ(EXTI4_IRQn);
    Firing_v_Handler();
    // Calculation_v_Handler();
    HAL_NVIC_EnableIRQ(EXTI4_IRQn);

    // HAL_GPIO_TogglePin(TestLED1_GPIO_Port,TestLED1_Pin);
}
#ifdef SENSOR_POLLING_MODE
static uint8_t IgnitionControl_FirstSensorCheck(void)
{
	uint8_t l_status = E_NOK;
	static uint8_t l_isSignalToggled = 0;

	if(0 == l_isSignalToggled)
	{
		if( GPIO_PIN_SET == HAL_GPIO_ReadPin(Signal_1_GPIO_Port, Signal_1_Pin) )
		{
			//signal debouncing time 256uS times the debounce multiplier value
			if(SIGNAL_DEBOUNCE_MULTIPLIER < g_uSDebouncingSignalCounter)
			{
				g_uSDebouncingSignalCounter = 0;
				if( GPIO_PIN_SET == HAL_GPIO_ReadPin(Signal_1_GPIO_Port, Signal_1_Pin) )
				{
					l_isSignalToggled = 1;
					//removed since sensor readout is used as RPM reference, not as firing angle signal
					//g_usSinceDetection = 0; //reset to zero to start calculating time to first cylinder firing
					g_FirstSensorTime_us = Calculate_u_Microseconds(g_uSCounter);
					l_status = E_OK;
					g_SignalFlag |=  1 << SENSOR_1_AVAILABLE;
					g_SyncFlag |= 1 << SENSOR_1_AVAILABLE;
					g_SensorActivationCounter++; //counter to measure how many times Signal occurred

					if(g_SignalState == 0)
					{
						g_FirstSensorTimePrevious_us = g_FirstSensorTime_us;
						g_SignalState = 1;
					}
					else if(g_SignalState == 1)
					{
						g_FirstSensorTimeCurrent_us = g_FirstSensorTime_us;
						g_SignalState = 2;
					}

				}
				else{}
			}
			else{}
		}
		else{}
	}
	if(GPIO_PIN_RESET == HAL_GPIO_ReadPin(Signal_1_GPIO_Port, Signal_1_Pin))
	{
		//To clear a BIT to have status when it is OFF
		l_isSignalToggled = 0;
		l_status = E_OK;
		g_SignalFlag &=  ~(1 << SENSOR_1_AVAILABLE);
	}
	else{}

	return l_status;
}
#endif /* SENSOR_POLLING_MODE */

extern void IgnitionControl_v_UpdateSignalTime(void)
{
	g_FirstSensorTime_us = Calculate_u_Microseconds(g_uSCounter);
	g_SignalFlag |=  1 << SENSOR_1_AVAILABLE;
	g_SyncFlag |= 1 << SENSOR_1_AVAILABLE;
	g_SensorActivationCounter++; //counter to measure how many times Signal occurred
    g_usSinceDetectionCyl1 = 0; // start time since detection of Signal
    GlobalDataValues.FiringState = en_FiringStateInactive; // reset the firing state for reseting the cranking firing.
    GlobalDataValues.isCylinder1CoilCharging = false;
    /* Check if the ignition coil is still active due to firing timer reset
     between activations at cranking RPM due to incosistent RPMS during cranking, 
     and if it so pin will go to reset to avoid damage to ignition coil. */
     if(true == HW_FiringPin_v_Cylinder_1_Status_Read())
     {
        HW_FiringPin_v_Cylinder_1_Reset();
     }

}
void IgnitionControl_v_UpdateSignalTimeCylinder2(void)
{
    g_SecondSensorTime_us = Calculate_u_Microseconds(g_uSCounter);
    g_SensorActivationCounterCylinder2++; //counter to measure how many times Signal occurred
    g_usSinceDetectionCyl2 = 0; // start time since detection of Signal
   // GlobalDataValues.FiringStateCylinder2 = en_FiringStateInactive; // reset the firing state for reseting the cranking firing.
    GlobalDataValues.isCylinder2CoilCharging = false;
    /* Check if the ignition coil is still active due to firing timer reset
     between activations at cranking RPM due to incosistent RPMS during cranking, 
     and if it so pin will go to reset to avoid damage to ignition coil. */
     if(true == HW_FiringPin_v_Cylinder_2_Status_Read())
     {
        HW_FiringPin_v_Cylinder_2_Reset();
     }  
}
extern uint8_t IgnitionControl_u_FirstSensorCheck_IT(void)
{
    static uint32_t l_g_SensorActivationCounter = 0U;

    /* Initial fetch of time at sensor first pulse */
	if ( (0U == g_SignalState)  && (1U == g_SensorActivationCounter) )
	{
		g_FirstSensorTimePrevious_us = g_FirstSensorTime_us;
		g_SignalState = 1U;
	}
    /* fetch of time at sensor second and future pulses */
	else if ( (g_SignalState == 1U) && (1U < g_SensorActivationCounter) && (l_g_SensorActivationCounter < g_SensorActivationCounter))
	{
		g_FirstSensorTimeCurrent_us = g_FirstSensorTime_us;
		g_SignalState = 2U;
        l_g_SensorActivationCounter = g_SensorActivationCounter;

	}


	return 0U;

}

extern uint8_t IgnitionControl_u_SecondSensorCheck_IT(void)
{
    g_SecondSensorTimeCurrent_us = g_SecondSensorTime_us;

    return 0U;

}


uint8_t IgntionControl_SyncCheck(void)
{
     uint8_t l_status = E_OK; 
     
     if( g_SyncFlag == (1 << SENSOR_1_AVAILABLE) )
     {
         g_SyncFlag = 0; //Clear the flag 
         l_status = E_OK;
         /*Sensor Activated 2 times */
         if( (2U <= g_SensorActivationCounter) && (g_FirstSensorTimePrevious_us != g_FirstSensorTimeCurrent_us) )
         {
              GlobalDataValues.SynchronizationStatus = IN_SYNC;
         }
         else
         {
             //do nothing
         }
     }
     else if( !(g_SyncFlag == (1 << SENSOR_1_AVAILABLE)) && (GlobalDataValues.SynchronizationStatus != OUT_OF_SYNC))
     {
         GlobalDataValues.SynchronizationStatus = OUT_OF_SYNC;
         g_LostSyncCounter++;
         l_status = E_NOK;
     }
     else 
     {
        // do nothing
     }
     return l_status; 
}
/* Data array for debug purposes */
volatile uint8_t g_LoggingGlobalDataArray[14] = {0};
static void Calculation_v_Handler(void)
{
    uint8_t l_Result = 0; 
    const uint16_t OneRevolutionAngleInDeg = 360; 
    const uint16_t SecondCylinderAngleinDeg = 225; // Odd firing angle at camshaft.
    volatile static uint32_t OneRevolutionTimeCylinder1 = 0;
    volatile static uint32_t OneRevolutionTimeCylinder2 = 0;
    volatile uint8_t AdvanceAngleCalculatedTime = 0;
    static uint8_t l_previousStateHandler = 0;
    volatile uint8_t l_PinStatus = 0U;
    /* Debug data output to uart */
    l_PinStatus = HW_FiringPin_v_Cylinder_1_Status_Read();
/*     memcpy(&g_LoggingGlobalDataArray[0],&GlobalDataValues.RPM,2U);
    memcpy(&g_LoggingGlobalDataArray[2],&GlobalDataValues.CalculationState,1U);
    memcpy(&g_LoggingGlobalDataArray[3],&GlobalDataValues.FiringState,1U);
    memcpy(&g_LoggingGlobalDataArray[4],&GlobalDataValues.TimeElapsedSinceDetection,4U);
    memcpy(&g_LoggingGlobalDataArray[8],&GlobalDataValues.FiringTimeCyl_1,4U);
    memcpy(&g_LoggingGlobalDataArray[12],&l_PinStatus,1U);
    memcpy(&g_LoggingGlobalDataArray[13],&GlobalDataValues.isCylinder1CoilCharging,1U);
    HAL_UART_Transmit(&huart2,g_LoggingGlobalDataArray,14U,10);
    HAL_UART_Transmit(&huart2,"\r\n",2U,10);  
    memset(g_LoggingGlobalDataArray,0U,14U);  */

    GlobalDataValues.Microseconds = Calculate_u_Microseconds(g_uSCounter);

    switch(GlobalDataValues.CalculationState)
    {
        case en_InitFinished:
        GlobalDataValues.CalculationState = en_SynchronizationOngoing;
        break;
        case    en_SynchronizationOngoing:
#ifdef SENSOR_INTERRUPT_MODE

        	IgnitionControl_u_FirstSensorCheck_IT();
            IgnitionControl_u_SecondSensorCheck_IT();
#else
        	l_Result = IgnitionControl_FirstSensorCheck();
#endif /*STM_INTERRUPT*/
        	l_Result = IgntionControl_SyncCheck();
        if( IN_SYNC == GlobalDataValues.SynchronizationStatus)
        {
             GlobalDataValues.CalculationState = en_Synchronized;

        }
        else
        {            //do nothing
        }
        break;

        case en_Synchronized:
    #ifdef SENSOR_INTERRUPT_MODE
                IgnitionControl_u_FirstSensorCheck_IT(); //OK
                IgnitionControl_u_SecondSensorCheck_IT();
    #else
                l_Result = IgnitionControl_FirstSensorCheck();
    #endif /*STM_INTERRUPT*/

        // Again check for uS values to get latest value for the check below
         GlobalDataValues.Microseconds = Calculate_u_Microseconds(g_uSCounter);
      	//If more than 2 Seconds have passed, disable the signal and set status to out of sync
         if( (MAX_TIME_FOR_SIGNAL_AVAILABILITY <= (GlobalDataValues.Microseconds - g_FirstSensorTimeCurrent_us))  )
     	{
     		g_SignalFlag &= ~(1 << SENSOR_1_AVAILABLE) ;
     		g_SyncFlag &= ~(1 << SENSOR_1_AVAILABLE) ;
     		GlobalDataValues.SynchronizationStatus = OUT_OF_SYNC;
     		GlobalDataValues.Microseconds = 0; //reset Microseconds counter to start from beginning to count the difference
     		GlobalDataValues.RPM = 0;
     		g_FirstSensorTimeCurrent_us = 0;
     		g_FirstSensorTimePrevious_us = 0;
            g_SecondSensorTimePrevious_us = 0;
            g_SecondSensorTimeCurrent_us = 0;
     		g_uSCounter = 0;
            g_LostSyncCounter++;
            g_RPMPrevTimeDifference_us = 0.0;
            g_RPM2PrevTimeDifference_us = 0.0;
            g_CrankingFiringFlag = 0U;
            GlobalDataValues.FiringState = en_FiringStateInactive;
            HW_FiringPin_v_Cylinder_1_Reset();
     	}
        /* First Cylinder RPM Calculation */
         if(g_FirstSensorTimeCurrent_us != g_FirstSensorTimePrevious_us)
        {
   
            GlobalDataValues.RPM = Calculate_u_RPM(CYLINDER_1, g_FirstSensorTimeCurrent_us, g_FirstSensorTimePrevious_us);
             /* Case when the RPM signal is already known, so we need just to update currentTime */
            if( 2 == g_SignalState )
            {
                g_FirstSensorTimePrevious_us = g_FirstSensorTimeCurrent_us;
                g_SignalState = 1;
            }
            else{}
            
            /* TODO: Add calculated rate of change of RPM with corresponding filtering until a good balance is achieved...*/
            if( (CRANKING_RPM >= GlobalDataValues.RPM) && (GlobalDataValues.RPM > 50U) ) 
            {
                GlobalDataValues.CalculationState = en_EngineCrankingCylinder1;
                g_CrankingFiringFlag = 0U;
             
            }
            if (CRANKING_RPM <  GlobalDataValues.RPM )
            {
                // GlobalDataValues.CalculationState = en_CalculationOngoing;
                /* Handling for case  of one cycle after higher rpm then cranking */
                if( 1U == g_CrankingFiringFlag )
                {
                    GlobalDataValues.CalculationState = en_EngineCrankingCylinder1; 
                    g_CrankingFiringFlag = 2U;               
                }
                else if (  0U == g_CrankingFiringFlag )
                {
                    GlobalDataValues.CalculationState = en_CalculationOngoing;
                }
    
              
            }
           
        }
         /* Second Cylinder RPM Calculation */
         if(g_SecondSensorTimeCurrent_us != g_SecondSensorTimePrevious_us)
        {
   
           GlobalDataValues.RPM2 = Calculate_u_RPM(CYLINDER_2, g_SecondSensorTimeCurrent_us, g_SecondSensorTimePrevious_us);
           g_SecondSensorTimePrevious_us = g_SecondSensorTimeCurrent_us;

           if( (CRANKING_RPM >= GlobalDataValues.RPM) && (GlobalDataValues.RPM > 50U) ) 
            {
                GlobalDataValues.CalculationState = en_EngineCrankingCylinder2;
            }
            else if (CRANKING_RPM <  GlobalDataValues.RPM )
            {
                GlobalDataValues.CalculationState = en_CalculationOngoing;
            }
        }


        if(3U == g_CrankingFiringFlag)
        {
            GlobalDataValues.CalculationState = en_CalculationOngoing;
            g_CrankingFiringFlag = 0U;
        }
            
        /* RPM Limiter will be implemented as a hard limiter, so if the RPMs are over 
        from setpoint, firing event will be skipped. */
        if (MAX_RPM <  GlobalDataValues.RPM )
        {
            GlobalDataValues.CalculationState = en_Synchronized;
            GlobalDataValues.FiringState = en_RPMHardLimitState;
            GlobalDataValues.FiringStateCylinder2 = en_RPMHardLimitState;
        }
        
        if( OUT_OF_SYNC == GlobalDataValues.SynchronizationStatus)
        {
            GlobalDataValues.CalculationState = en_SynchronizationOngoing;
        }

     
        break;

        case en_CalculationOngoing:
            // 1. Get the Advance angle
#ifdef USING_ADVANCE_TIMING
        	GlobalDataValues.AdvanceAngle = get_u_AdvanceAngle(GlobalDataValues.RPM);
            AdvanceAngleCalculatedTime =  CalculateTime_u_FromAngle(GlobalDataValues.RPM, GlobalDataValues.AdvanceAngle);
#endif /*USING_ADVANCE_TIMING*/
#ifdef  USING_FIXED_TIMING
        	GlobalDataValues.AdvanceAngle = FIXED_TIMING_ANGLE;
            AdvanceAngleCalculatedTime =  CalculateTime_u_FromAngle(GlobalDataValues.RPM, GlobalDataValues.AdvanceAngle);
#endif /*USING_FIXED_TIMING*/

            OneRevolutionTimeCylinder1 =  CalculateTime_u_FromAngle(GlobalDataValues.RPM, (OneRevolutionAngleInDeg - IGNITION_STATIC_ADVANCE_ANGLE) );
          // 2. Calculate Firing time Cyl-1
           GlobalDataValues.FiringTimeCyl_1 = Calculate_u_FiringTimeCylinder(AdvanceAngleCalculatedTime, OneRevolutionTimeCylinder1);
           /* 2.1  Rate of change of Firing time - to be seen if it is beneficial */
          // GlobalDataValues.FiringTimeCyl_1 = CalculateRate_u_OfChange(&g_PrevTimeDifference_us, GlobalDataValues.FiringTimeCyl_1);
            // 3. Calculate Firing time Cyl-2
           GlobalDataValues.FiringTimeCyl_2 = GlobalDataValues.FiringTimeCyl_1;
            // 4. set state to en_CalculationFinished

            if( (0 < GlobalDataValues.FiringTimeCyl_1) && (0 < GlobalDataValues.FiringTimeCyl_2))
            {
            GlobalDataValues.CalculationState = en_CalculationFinished;
            }

            break;
        case en_CalculationFinished:
        	 GlobalDataValues.CalculationState = en_Synchronized;
        	 GlobalDataValues.FiringState = en_FiringCylinder1;
             GlobalDataValues.FiringStateCylinder2 = en_FiringCylinder2;
            break;
        case en_IdleStateCalculation:
            //do nothing 
            break;
        case en_EngineCrankingCylinder1:
            GlobalDataValues.CalculationState = en_Synchronized;
            GlobalDataValues.FiringState = en_FiringCylinder1Cranking;
            break;
            case en_EngineCrankingCylinder2:
            GlobalDataValues.CalculationState = en_Synchronized;
            GlobalDataValues.FiringStateCylinder2 = en_FiringCylinder2Cranking;
            break;
        default: 
            // should not be reached.
            break; 
                   
    }
    
 
    
}

static void Firing_v_Handler(void)
{
  
    
  /*NOTE: PROVE at integration test level if no race condition will occur during
    firing of both cylinders due to faulty handling in FSM or time overlaps
    Additional idea, put both handlers inside of 1 case en_FiringCylinders...*/
   
	 GlobalDataValues.TimeElapsedSinceDetectionCylinder1 = g_usSinceDetectionCyl1 * 10;
     GlobalDataValues.TimeElapsedSinceDetectionCylinder2 = g_usSinceDetectionCyl2 * 10;

        switch(GlobalDataValues.FiringState)
        {
            case en_FiringCylinder1Cranking:
                if(CRANKING_RPM >=  GlobalDataValues.RPM )
                {
                    g_CrankingFiringFlag = 1U;
                }
                Firing_v_Cylinder1Cranking();
            break;
            case en_FiringCylinder1:
                Firing_v_Cylinder1();
            break;
            case en_FiringCylinder1Completed:
                GlobalDataValues.FiringState = en_IdleStateFiringState;
              
            break;
            case en_RPMHardLimitState:
                GlobalDataValues.FiringState = en_IdleStateFiringState;
            break;
            case en_IdleStateFiringState:
             // do nothing
            break;
            default:
             // should not be reached.
            break;
        }

        switch(GlobalDataValues.FiringStateCylinder2)
        {
            case en_FiringCylinder2Cranking:
                Firing_v_Cylinder2Cranking();
            break;
            case en_FiringCylinder2:
                Firing_v_Cylinder2();
            break;
            case en_FiringCylinder2Completed:
            GlobalDataValues.FiringStateCylinder2 = en_IdleStateFiringState;
            break;
            case en_RPMHardLimitState:
            GlobalDataValues.FiringStateCylinder2 = en_IdleStateFiringState;
            case en_IdleStateFiringState:
            // do nothing 
            break;
            default:
            // should not be reached.
            break; 
        }
   
}


extern uint16_t Calculate_u_RPM(uint8_t in_Cylinder, uint32_t in_CurrentTime, uint32_t in_PrevTime)
{
    uint16_t l_CalculatedRPM = 0;
    const double alpha = 0.5;
    volatile double l_TimeDifference_us = 0.0;
    volatile double l_TimeDifference_ms = 0.0;
    volatile  double l_AngularVelocity = 0.0; 
    volatile double l_DeltaTimeDifference_us = 0.0;
    
 l_TimeDifference_us = (in_CurrentTime - in_PrevTime);
 if(CYLINDER_1 == in_Cylinder)
{
    l_DeltaTimeDifference_us = alpha * (l_TimeDifference_us - g_RPMPrevTimeDifference_us);
    g_RPMPrevTimeDifference_us = l_TimeDifference_us;
}
else if(CYLINDER_2 == in_Cylinder)
{
    l_DeltaTimeDifference_us = alpha * (l_TimeDifference_us - g_RPM2PrevTimeDifference_us);
    g_RPM2PrevTimeDifference_us = l_TimeDifference_us;
}
else
{
    // do nothing 
}
 
 /* Calculated rate of change */
 l_TimeDifference_us += l_DeltaTimeDifference_us;
 l_TimeDifference_ms = l_TimeDifference_us / 1000.0f; 
 l_AngularVelocity = (2.0 * M_PI * 1000.0) /(l_TimeDifference_ms ); //[rad/S]
 l_CalculatedRPM = (uint16_t) (l_AngularVelocity * 30.0f / M_PI); 
// Linear fltering - not good try with moving average if the rate of change is not functioning as it should be....
//l_CalculatedRPM =  (uint16_t) (alpha * l_CalculatedRPM  + (1.0 - alpha) * GlobalDataValues.RPM);

#ifdef USING_CRANK_SIGNAL
 return      l_CalculatedRPM;
#endif/*USING_CRANK_SIGNAL*/
#ifdef USING_CAM_SIGNAL
 return      l_CalculatedRPM * 2 ;
#endif/*USING_CAM_SIGNAL*/
}

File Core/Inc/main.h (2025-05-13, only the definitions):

#define PC14_OSC32_IN_Pin GPIO_PIN_14
#define PC14_OSC32_IN_GPIO_Port GPIOC
#define PC15_OSC32_OUT_Pin GPIO_PIN_15
#define PC15_OSC32_OUT_GPIO_Port GPIOC
#define PH0_OSC_IN_Pin GPIO_PIN_0
#define PH0_OSC_IN_GPIO_Port GPIOH
#define PH1_OSC_OUT_Pin GPIO_PIN_1
#define PH1_OSC_OUT_GPIO_Port GPIOH
#define ADC_VMCU_Pin GPIO_PIN_1
#define ADC_VMCU_GPIO_Port GPIOA
#define ADC_VSENS_Pin GPIO_PIN_2
#define ADC_VSENS_GPIO_Port GPIOA
#define ADC_VBAT_Pin GPIO_PIN_3
#define ADC_VBAT_GPIO_Port GPIOA
#define Signal1_IntPin_Pin GPIO_PIN_4
#define Signal1_IntPin_GPIO_Port GPIOA
#define Signal1_IntPin_EXTI_IRQn EXTI4_IRQn
#define ADC_IGNITION_Pin GPIO_PIN_0
#define ADC_IGNITION_GPIO_Port GPIOB
#define Signal2_IntPin_Pin GPIO_PIN_10
#define Signal2_IntPin_GPIO_Port GPIOE
#define Signal2_IntPin_EXTI_IRQn EXTI15_10_IRQn
#define Cylinder4Out_Pin_Pin GPIO_PIN_11
#define Cylinder4Out_Pin_GPIO_Port GPIOB
#define Cylinder3Out_Pin_Pin GPIO_PIN_12
#define Cylinder3Out_Pin_GPIO_Port GPIOB
#define TestLED2_Pin GPIO_PIN_13
#define TestLED2_GPIO_Port GPIOB
#define TestLED1_Pin GPIO_PIN_14
#define TestLED1_GPIO_Port GPIOB
#define SPI1_CS_Pin GPIO_PIN_8
#define SPI1_CS_GPIO_Port GPIOA
#define OE_PIN1_Pin GPIO_PIN_9
#define OE_PIN1_GPIO_Port GPIOA
#define OE_PIN2_Pin GPIO_PIN_10
#define OE_PIN2_GPIO_Port GPIOA
#define SWDIO_Pin GPIO_PIN_13
#define SWDIO_GPIO_Port GPIOA
#define SWCLK_Pin GPIO_PIN_14
#define SWCLK_GPIO_Port GPIOA

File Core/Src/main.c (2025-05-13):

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
/* Includes ------------------------------------------------------------------*/
#include "main.h"

/* USER CODE BEGIN Includes */
#include "core_cm4.h"
/* USER CODE END Includes */

/* USER CODE BEGIN PD */
#define DEMCR           (*((volatile uint32_t*)0xE000EDFCU))
#define ITM_STIM_PORT0  (*((volatile uint32_t*)0xE0000000U))
#define ITM_TCR         (*((volatile uint32_t*)0xE0000E80U))
#define ITM_TER         (*((volatile uint32_t*)0xE0000E00U))
#define TPIU_ACPR       (*((volatile uint32_t*)0xE0040010))
/* USER CODE END PD */

ADC_HandleTypeDef hadc1;

CAN_HandleTypeDef hcan1;

I2C_HandleTypeDef hi2c1;

SPI_HandleTypeDef hspi1;

TIM_HandleTypeDef htim2;
TIM_HandleTypeDef htim3;

UART_HandleTypeDef huart3;

void SystemClock_Config(void);
static void MX_GPIO_Init(void);
static void MX_TIM2_Init(void);
static void MX_CAN1_Init(void);
static void MX_I2C1_Init(void);
static void MX_SPI1_Init(void);
static void MX_USART3_UART_Init(void);
static void MX_ADC1_Init(void);
static void MX_TIM3_Init(void);
/* USER CODE BEGIN PFP */
void init_swo(uint32_t baudrate) {
  // Enable debug tracing
  *((volatile uint32_t*)0xE000EDFC) |= (1 << 24);  // DEMCR |= TRCENA;

  // Set the SWO baud rate
  *((volatile uint32_t*)0xE0040010) = (SystemCoreClock / baudrate) - 1;  // TPIU_ACPR

  // Enable NRZ mode
  *((volatile uint32_t*)0xE00400F0) = 0x00000002;  // TPIU_SPPR

  // Enable ITM Stimulus Port 0
  *((volatile uint32_t*)0xE0000E00) = 0x00000001;  // ITM_TER
}
void ITM_SendChar2(uint8_t ch) {
    // Enable TRCENA in DEMCR
    DEMCR |= (1 << 24);
    // Enable ITM
   // ITM_TCR = 0x0001000D;
    // Enable stimulus port 0
    ITM_TER |= (1 << 0);
    // Wait for FIFO to be ready
    while (!(ITM_STIM_PORT0 & 1));
    // Send character
    ITM_STIM_PORT0 = ch;
}

void check_swo_baudrate() {
  uint32_t prescaler = TPIU_ACPR + 1; // ACPR holds (Prescaler - 1)
  volatile uint32_t swo_baudrate = SystemCoreClock / prescaler;
  printf("SWO Baudrate: %lu Hz\n", swo_baudrate);
}
/* USER CODE END PFP */

/**
  * @brief  The application entry point.
  * @retval int
  */
int main(void)
{
  /* MCU Configuration--------------------------------------------------------*/

  /* Reset of all peripherals, Initializes the Flash interface and the Systick. */
  HAL_Init();

  /* Configure the system clock */
  SystemClock_Config();

  /* Initialize all configured peripherals */
  MX_GPIO_Init();
  MX_TIM2_Init();
  MX_CAN1_Init();
  MX_I2C1_Init();
  MX_SPI1_Init();
  MX_USART3_UART_Init();
  MX_ADC1_Init();
  MX_TIM3_Init();
  /* USER CODE BEGIN 2 */
  HAL_TIM_Base_Start_IT(&htim2);
  IgnitionCtrl_v_Init();

 // init_swo(42U);
  /* USER CODE END 2 */

  /* Infinite loop */
  /* USER CODE BEGIN WHILE */
  while (1)
  {
    /* USER CODE END WHILE */

    /* USER CODE BEGIN 3 */

    IgnitionControl_v_Main();
/*    HAL_GPIO_TogglePin(TestLED1_GPIO_Port,TestLED1_Pin);
   HAL_GPIO_TogglePin(TestLED2_GPIO_Port,TestLED2_Pin);
  HAL_GPIO_TogglePin(LD3_GPIO_Port,LD3_Pin);
  HAL_GPIO_TogglePin(LD4_GPIO_Port,LD4_Pin); 
  HAL_Delay(500U); */
  }
  /* USER CODE END 3 */
}

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


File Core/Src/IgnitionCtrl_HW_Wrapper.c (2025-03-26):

/**
 * @file      IgnitionCtrl_HW_Wrapper.c
 * @authors   Miroslav Mitrovic
 * Created on September 16, 2022, 7:33 PM
 * @Copyright 2022 by Miroslav Mitrovic <mmitrovicmas13@gmail.com>
 *
 * This file is part of open source application.
 * 
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
 * @license GPL-3.0+ <http://spdx.org/licenses/GPL-3.0+>
 *
 * @brief [description]
 */
/*******************************************************************************
 * Includes
 *******************************************************************************/
#include "IgnitionCotrol_Main.h"
/*******************************************************************************
 * Defines
 *******************************************************************************/

/*******************************************************************************
 * Local Types and Typedefs
 *******************************************************************************/

/*******************************************************************************
 * Global Variables
 *******************************************************************************/
 volatile uint32_t g_usSinceDetectionCyl1;
 volatile uint32_t g_usSinceDetectionCyl2;
 volatile uint32_t g_uSCounter;
 volatile uint32_t g_uSDebouncingSignalCounter;
 volatile uint8_t  g_signalDebouncingTimerStarted;
/*******************************************************************************
 * Static Function Prototypes
 *******************************************************************************/

/*******************************************************************************
 * Static Variables
 *******************************************************************************/

/*******************************************************************************
 * Functions
 *******************************************************************************/
void HW_GPIO_v_Init(void)
{
#ifdef ATMEL_MCU
  /*Set Pins 5 and 6 as Output High */
DDRB |= ((1 << PB1) | (1 << PB0) | (1 << PB2) | (1 << PB3) | (1 << PB4)) | (1 << PB5);
/*Set Pins 3 and 2 as Input pins*/
DDRB &= (~(1 << PB3) & ~(1 << PB2) );
DDRB |= (1 << PB4);
PORTB &= ~(1 << PB1 );
PORTB &= ~(1 << PB0 );
#else
/*TODO: Implement STM32Fxx handling of GPIO INIT*/
#endif /*ATMEL_MCU*/
}

void HW_Timer_v_Init(void)
{
#ifdef ATMEL_MCU
    TCCR0B |= (1 << CS00);   	//Select the clock source-Internal Oscillator clk_io/8 = 1MHz ClockDivider is C00(no divsion) - overflow happens at 256uS(counts)
	TCNT0 = 0;
	TIMSK |=  (1 << TOIE0);				//Enable Timer0 overflow interrupt
#else
/*TODO: Implement STM32Fxx handling of Timer INIT*/
#endif /*ATMEL_MCU*/
	g_uSCounter = 0;
	g_usSinceDetectionCyl1 = 0;
	g_uSDebouncingSignalCounter = 0;
}

void HW_FiringPin_v_Cylinder_1_Set(void)
{
#ifdef ATMEL_MCU
	PORTB |= ( 1<< PB1);
#else
	// HAL_GPIO_WritePin(GPIOD, LD4_Pin, GPIO_PIN_SET);
	HAL_GPIO_WritePin(TestLED1_GPIO_Port, TestLED1_Pin, GPIO_PIN_SET);
#endif /*ATMEL_MCU*/


}

void HW_FiringPin_v_Cylinder_1_Reset(void)
{
#ifdef ATMEL_MCU
    PORTB &= ~( 1<< PB1);
#else
	// HAL_GPIO_WritePin(GPIOD, LD4_Pin, GPIO_PIN_RESET);
	HAL_GPIO_WritePin(TestLED1_GPIO_Port, TestLED1_Pin, GPIO_PIN_RESET);
#endif /*ATMEL_MCU*/
}

void HW_FiringPin_v_Cylinder_2_Set(void)
{
#ifdef ATMEL_MCU
	PORTB |= ( 1<< PB0);
#else
	HAL_GPIO_WritePin(TestLED2_GPIO_Port, TestLED2_Pin, GPIO_PIN_SET);
#endif /*ATMEL_MCU*/
}

void HW_FiringPin_v_Cylinder_2_Reset(void)
{
#ifdef ATMEL_MCU
    PORTB &= ~( 1<< PB0);
#else
	HAL_GPIO_WritePin(TestLED2_GPIO_Port, TestLED2_Pin, GPIO_PIN_RESET);
#endif /*ATMEL_MCU*/
}

GPIO_PinState HW_FiringPin_v_Cylinder_1_Status_Read(void)
{
	return	HAL_GPIO_ReadPin(TestLED1_GPIO_Port,TestLED1_Pin);
}

GPIO_PinState HW_FiringPin_v_Cylinder_2_Status_Read(void)
{
	//HAL_GPIO_ReadPin(TestLED1_GPIO_Port,TestLED1_Pin);
}

#ifdef STM32_MCU
void HAL_GPIO_EXTI_Callback(uint16_t GPIO_Pin)
{
	/* Prevent unused argument(s) compilation warning */
	if(Signal1_IntPin_Pin == GPIO_Pin)
	{
		if(5U < g_uSDebouncingSignalCounter) /* Check if the signal was triggered in time less than 50uS */
		{
			IgnitionControl_v_UpdateSignalTime();
	/* 		g_uSDebouncingSignalCounter = 0;
			g_signalDebouncingTimerStarted = 1; */
		}
	}
	else if (Signal2_IntPin_Pin == GPIO_Pin)
	{
		if(5U < g_uSDebouncingSignalCounter) /* Check if the signal was triggered in time less than 50uS */
		{
			IgnitionControl_v_UpdateSignalTimeCylinder2();
			g_uSDebouncingSignalCounter = 0;
			g_signalDebouncingTimerStarted = 1;
			
		}
	}
	else{}
  /* NOTE: This function Should not be modified, when the callback is needed,
           the HAL_GPIO_EXTI_Callback could be implemented in the user file
   */
}
#endif /* STM32_MCU */

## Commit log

2022-12-23 Implemented First Cylinder Firing
2023-02-28 Added Dynamic Tests-GTest Framework
2023-03-25 removal of STM32CubeIDE files
2023-03-25 Updates to STM32Cube IOC file
2023-10-07 MCU datasheet,reference manual and HAL&LL Driver description
2023-10-07 Updates to gitignore file, added build folder of GTest Framework
2023-10-07 removal of GTest Framework build files
2023-10-07 "Configured SigPin1 and SigPin2 as Interrupts.
2025-03-02 Implemented firing logic for engine cranking case
2025-03-16 Fix for cranking handling
    [IgnitionController.ioc, IgnitionCotrol_Main.c, IgnitionCtrl_HW_Wrapper.c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]
2025-03-19 Fixes for handling Transition
    [IgnitionCotrol_Main.c]
2025-03-20 Configuration and RPM filtering fixes
    [IgnitionCotrol_Main.c, IgnitionCtrl_Config.h]
2025-03-26 2nd Cylinder Cranking Implementation
2025-03-29 Implemented proper 2nd cylinder firing logic
2025-04-23 PowerSupply Initial Sch
    [IgnitionController.kicad_pcb, IgnitionController.kicad_sch, IgnitionController_PowerSupply.kicad_sch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]
2025-04-27 PMIC HW implementation
    [Connector.kicad_sch, IgnitionController.kicad_sch, IgnitionDriver.kicad_sch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]
2025-04-28 Updated sch and footprints
    [PMIC.kicad_sch, untitled.kicad_sch]
2025-05-01 MCU sheet Initial commit
    [MCU.kicad_sch, untitled.kicad_sch]
2025-05-03 Peripherals Update
    [IgnitionDriver.kicad_sch, MCU.kicad_sch, PMIC.kicad_sch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]
2025-05-13 Updates to HW Layout
    [770669-1.stp, 7706691.psm, Connector.kicad_sch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]
2025-05-24 Initial routing of Power supply
    [Fuel_Injector_Drivers.kicad_sch, IgnitionController.kicad_pcb, IgnitionDriver.kicad_sch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]
2025-06-07 Added Crystal to PMIC
    [IgnitionController.kicad_pcb, untitled.kicad_sch]
2025-06-07 MCU HW Initial Layout
    [IgnitionController.kicad_pcb, MCU.kicad_sch]
2025-06-08 Added Peripheral HW Components
    [IgnitionController.kicad_pcb, untitled.kicad_sch]
2025-06-08 Routing PCB done
    [IgnitionController.kicad_pcb, Peripherals.kicad_sch]
2025-06-08 Updated Solder Mask labels
    [Connector.kicad_sch, IgnitionController.kicad_pcb, MCU.kicad_sch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]
2025-06-12 Addition of 3d model of ECU
    [Body.step.SLDPRT, IgnitionController.kicad_pcb, Pins.step.SLDPRT]

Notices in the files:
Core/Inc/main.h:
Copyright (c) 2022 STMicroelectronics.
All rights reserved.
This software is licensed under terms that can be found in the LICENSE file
